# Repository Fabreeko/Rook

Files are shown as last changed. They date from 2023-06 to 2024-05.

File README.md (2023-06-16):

# Rook_Fabreeko
Fabreeko Rook Kit 

https://www.fabreeko.com/products/rook-mk1-by-rolohaun-3d-pre-order?_pos=1&_psq=Roo&_ss=e&_v=1.0

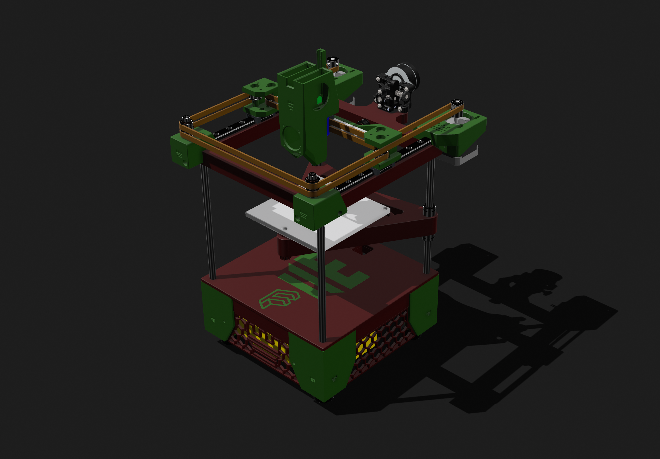
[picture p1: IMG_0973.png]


a derivative of the great work by https://github.com/rolohaun/Rook

We encourage you to use an Initial Startup process like https://docs.vorondesign.com/build/startup/ once you first turn it on. If the stepper_buzz process doesn't yield expected results, you may need to swap the center two wires at one end (I did the motor end) of the wire harness. 

Discord: https://discord.gg/MnxdJcBk

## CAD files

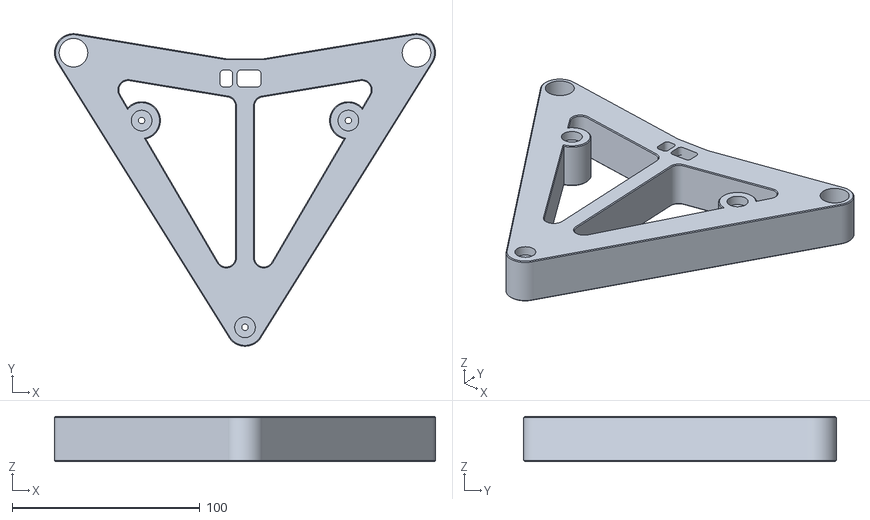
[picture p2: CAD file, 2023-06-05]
STLs/Bed support/Main Bed support.stl
202.7 x 166.3 x 24.0

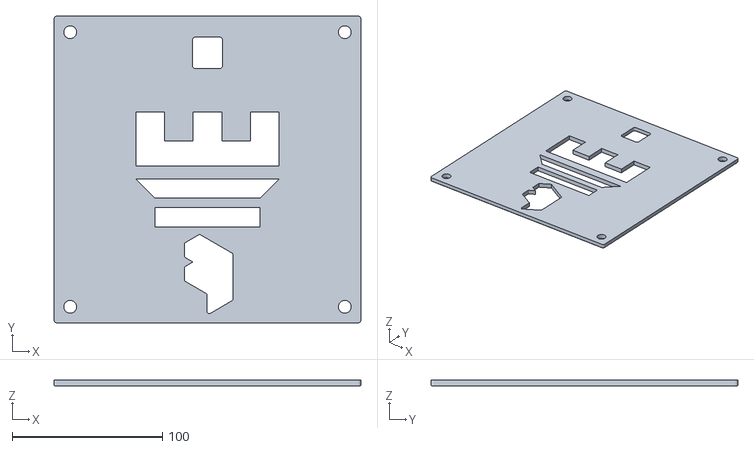
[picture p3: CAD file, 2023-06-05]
STLs/panel/Main panel.stl
204.0 x 204.0 x 4.00

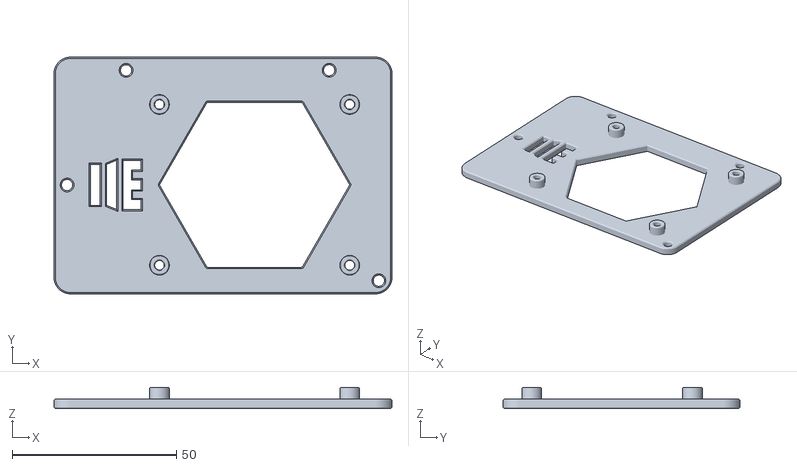
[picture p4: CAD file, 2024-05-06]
STLs/bottom frame/BTT_SKR_E3_v3_to_SKR_Pico_Mount_STL.stl
103.0 x 72.1 x 6.50

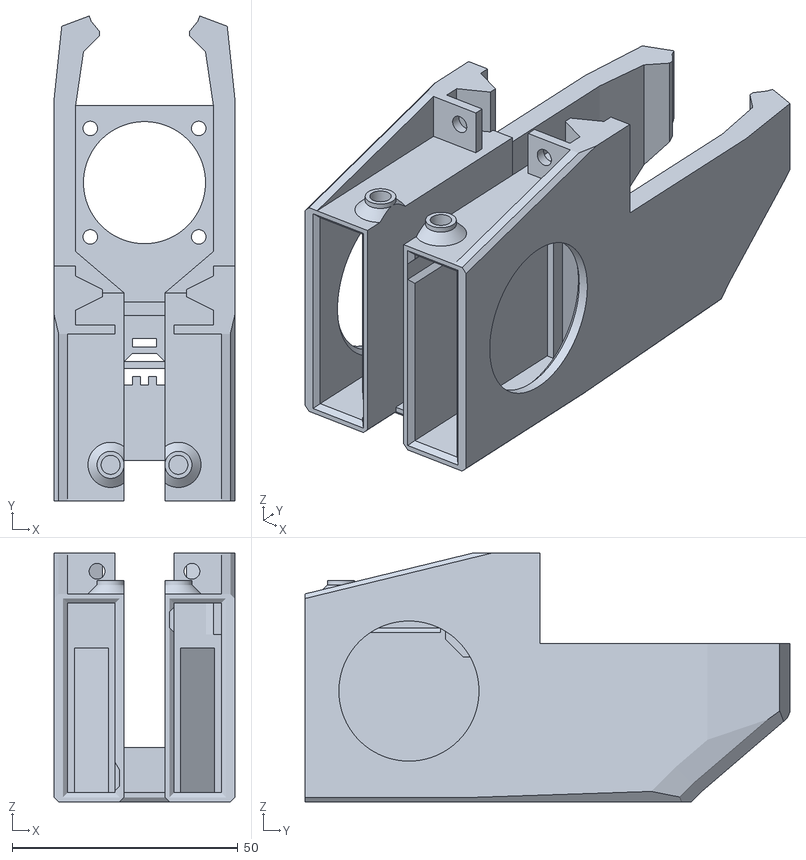
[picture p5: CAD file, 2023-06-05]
STLs/gantry/(a) Cowling.stl
40.0 x 107.3 x 55.0

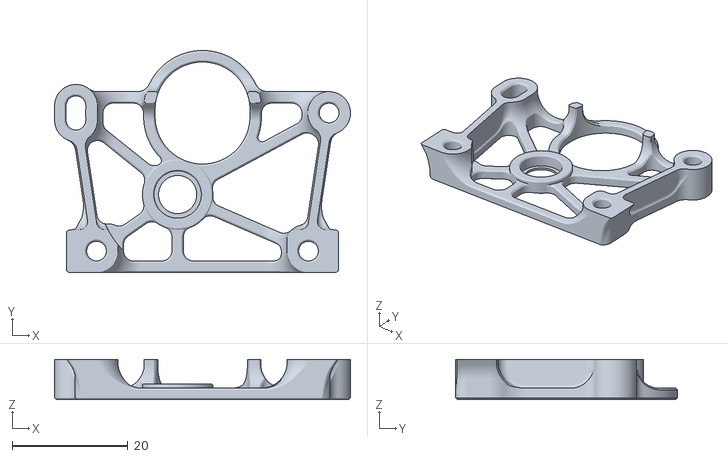
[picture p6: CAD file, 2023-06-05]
STLs/mini Sherpa/Housing rear.stl
51.2 x 38.4 x 7.00

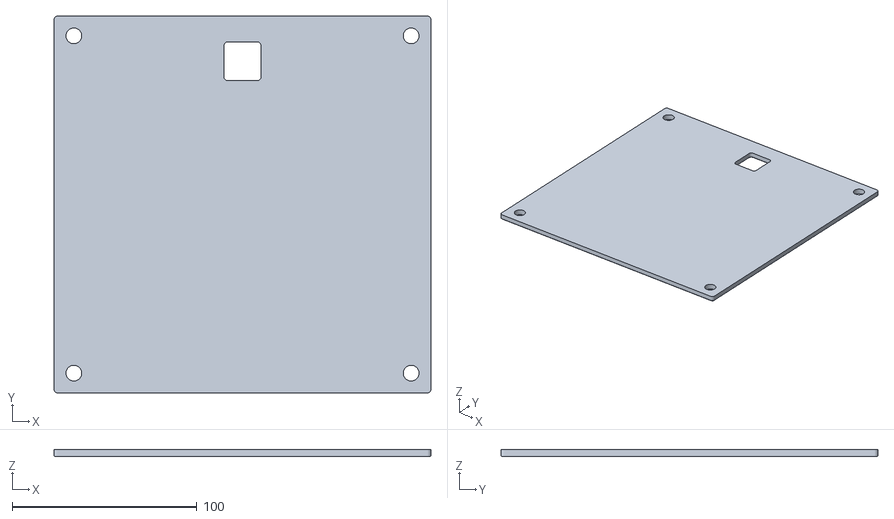
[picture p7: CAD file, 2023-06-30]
STLs/panel/Rook MMU Panel.stl
204.0 x 204.0 x 4.00

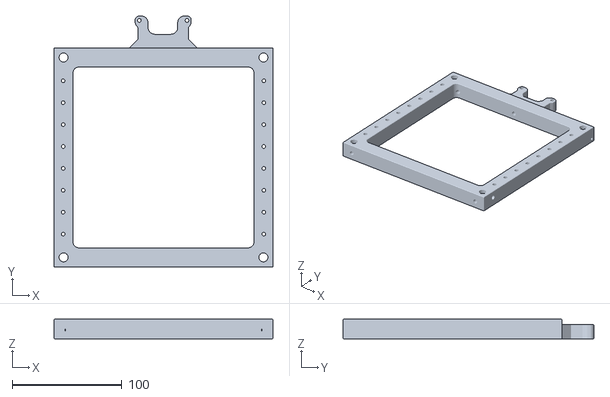
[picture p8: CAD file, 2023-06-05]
STLs/Top Frame/top frame.stl
200.0 x 229.1 x 18.0

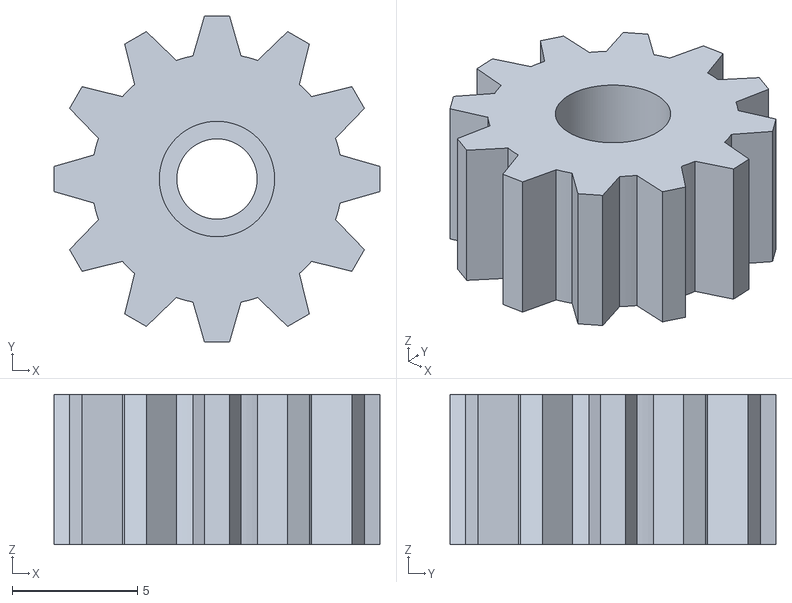
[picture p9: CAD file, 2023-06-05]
STLs/Bed support/Thumb wheelx3.stl
13.0 x 13.0 x 6.00

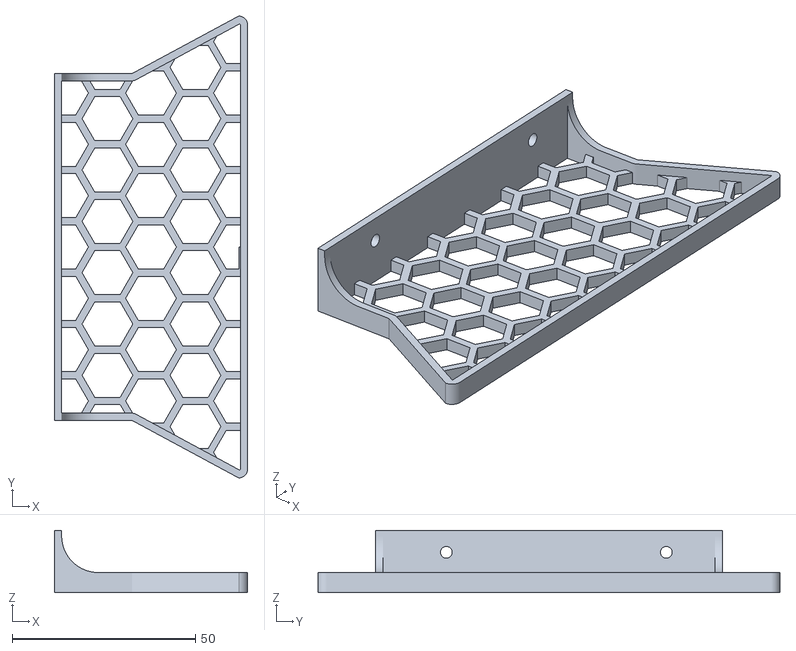
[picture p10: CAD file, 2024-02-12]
STLs/bottom frame/ b_side skirt.stl
52.7 x 126.0 x 17.0

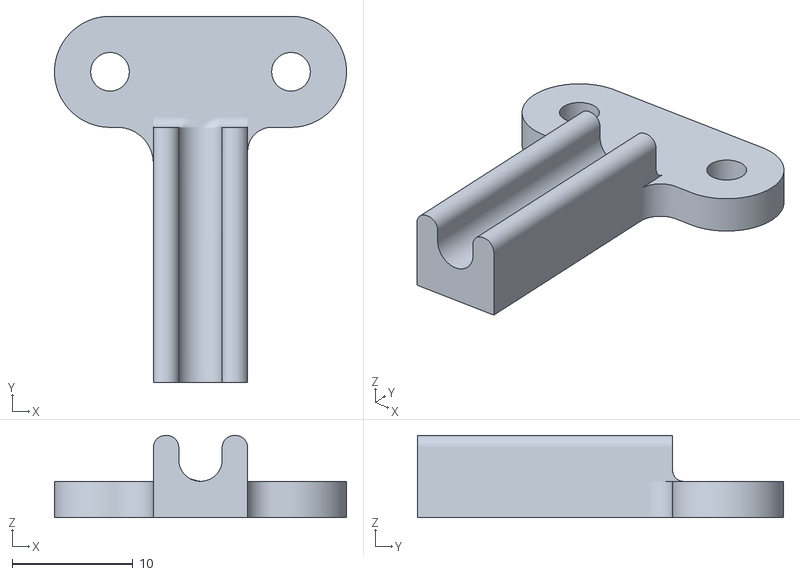
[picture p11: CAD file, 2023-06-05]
STLs/gantry/(a) Stress relief.stl
24.2 x 30.4 x 6.80

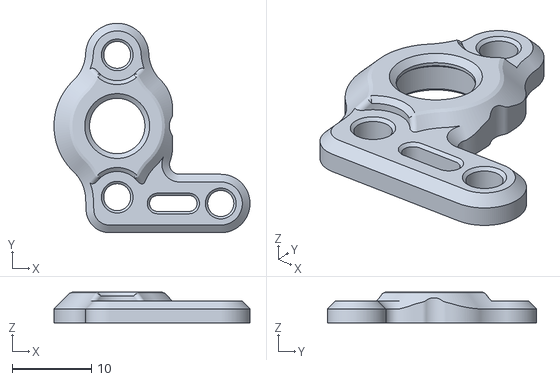
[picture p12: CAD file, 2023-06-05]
STLs/mini Sherpa/(a) Housing front.stl
24.8 x 26.5 x 3.90

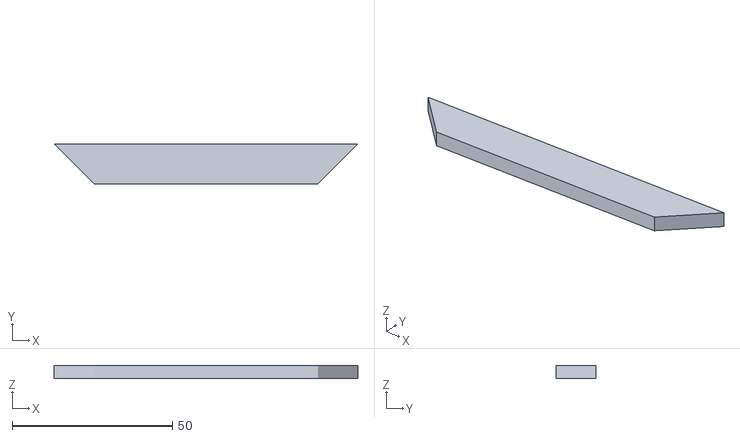
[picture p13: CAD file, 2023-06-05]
STLs/panel/(a) logo_mid.stl
94.8 x 12.5 x 4.00

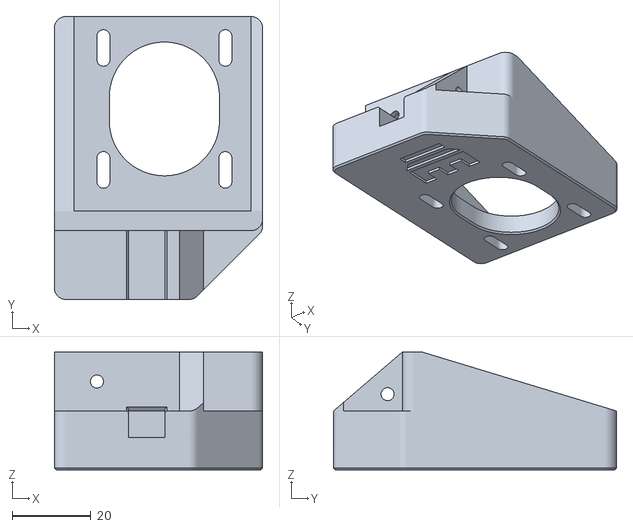
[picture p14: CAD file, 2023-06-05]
STLs/Top Frame/(a) B motor mount.stl
53.0 x 72.0 x 30.0

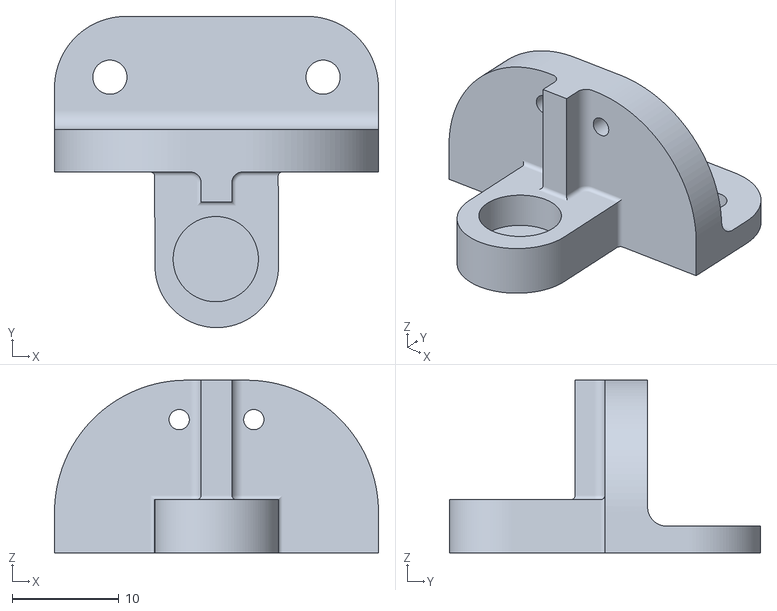
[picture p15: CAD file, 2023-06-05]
STLs/Bed support/Z endstop bracket .stl
30.4 x 29.2 x 16.2

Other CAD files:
STLs/bottom frame/(a) Front left leg.stl
STLs/gantry/(a) Belt clamp.stl
STLs/mini Sherpa/(a) idler arm long.stl
STLs/panel/F Insert 3.stl
STLs/Top Frame/(a) A motor mount.stl
STLs/Top Frame/(a) Gantry.stl
STLs/Top Frame/(a) Left idler mount.stl
STLs/Top Frame/(a) Right idler mount.stl
STLs/bottom frame/(a) Back Left leg.stl
STLs/bottom frame/(a) Front right leg.stl
STLs/bottom frame/(a)Back right leg.stl
STLs/bottom frame/b_Front skirt.stl
STLs/gantry/(a) Hotend Mount.stl
STLs/panel/(a) F Insert 5.stl
STLs/panel/(a) logo_bottom.stl
STLs/panel/(a) logo_top.stl
STLs/panel/F Insert 1.stl
STLs/panel/F Insert 2.stl
STLs/panel/F Insert 4.stl

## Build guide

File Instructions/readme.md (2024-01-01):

# Rook MK1 By Rolohaun 3D
---
### Time to get started! 

Ok - time to take a break.  Go to a different room where you can't see or touch a single piece of the printer. Grab a refreshment, sit down and read through this all the way to the bottom. Once you have read all the way through it, and come back to this point, you can return to the printer. Remember, your camera is on and we can see if you don't do this!

First step is to get all of the heat sets placed. There are 2 different sized heatsets in the kit. Its important to use the shorter heatsets on the rookery and mounting key. If you are not familiar with this, Nero3D has a couple of good YouTube videos on it. 
https://youtube.com/shorts/cyof7fYFcuQ?feature=share

 ### Start by placing heatsets into the lower frame:

Step1

 ### Then place them into the Bed Support, dont forget to place them in the thumbscrews as well (not pictured)



 ### Next, the upper frame



 ### ...and finally, the tool head parts



 ### Next up is attaching the feet to the legs. 
 An M5 nut is captured in the leg and 4 M5X16 SHCS attach the feet.



 ### Attach all four feet to the lower frame as shown using 8 M3x10 SHCS. 



 ### Stand the printer up and insert the four 8mm rods into place. 



 ### This is your first "square and level check". 
 On a known flat surface, make sure the feet don't wobble. Flip it to stand upside down and check for wobbles. This makes sure all the rods are inserted evenly. 
 Grab the lower panel and the inserts. This should be a nice snug fit that can be tapped into place. Assemble all pieces. 



 ### Drop the panel down over the rods. 
 Pay attention to orientation here. 



 ### Insert the bearings into the bed support and center them. 
 They are extra long on purpose to provide more support. Attach the Z endstop in place using two M3x6 SHCS. 



 ### Lower the bed support onto the rear 8mm rods as shown. Note that the Z endstop faces down. 



 ### Attach Y rails to the top frame with 16 M3x20 SHCS. 
 Leave the shuttle keepers in place for now.



 ### Place the top frame on top of the 8mm rods. 
 Make sure it bottoms out on the rods.



 ### Place motor mounts and front idlers on top frame. 
 Two M3x16 BHCS (one each) go in the idlers from the front.  Two M3x10 (one each) attach them from the sides. Two M3X8 SHCS (one each) attach the motor mount from the side into the plastic (be careful not to overtighten/strip these). Two M3x18 SHCS (one each) attach the mount from the rear. 


 ### Attach the linear rail to the X axis.
 Attach the rail to the x-axis using eight M3X12 BHCS with a washer and M3 nut on the back of each. Don't let the shuttle fall of the ends! 



 ### Attach the X axis to the Y rails.
 Attach using three M3x6 SHCS on each side (six total). 



 ### Attach the A/B motors
 Attach the motors to the motor mounts with four M3x10 SHCS (eight total), adjusted all the way towards the front of the printer.  Wires go towards the center. Attach the GT2 pulleys as shown. Pay attention to orientation and height. We will fine tune the height later.


 ### This shows a proper bearing stack assembly for a double bearing stack.  
 Note the two shims in the middle. Always do shim-bearing-bearing-shim on a single. A double is two singles so two shims in the middle. 


 ### Install four single bearing stacks in the X axis using M5x25 SHCS. 





 ### ...and a double bearing stack on each idler using M5x30 SHCS. 


 ### ...and a single stack for the Z belt using an M5x20 SHCS.



 ### The belt path is a standard CoreXY belt path. Study the two pics carefully. One is a cut away and the other is a normal view.  Being methodical here will pay off in the long run. 





 ### Install the Belt Clamp
We will be taking the mount on and off a couple times. It attaches using 4 M3x6 BHCS. The first step will use the full length of the supplied belt. With the teeth facing front, insert one end of the belt through the back of the mounting plate throught the top, right side yellow hole of the blue part in the picture. Fold the belt back over itself so about 25mm overlaps, teeth to teeth. Use a wire tie to temporarily secure it. (Note: my CAD skills and time did not allow me to show the belt loop or teeth so follow the words, not just the picture) 


-  Using the picture above, route the other end through the top belt path all the way around and back through the top left hole from behind.
  - Pull snug and temporarily secure the belt back onto itself.
  - Carefully review your work while looking at the belt path in the picture. Make sure the belt is riding properly on each beating. 

- Cut the belt about 25mm past the securing point. (So you have an extra 25mm). 

- Completely remove the belt.  
  - Lay the piece you just cut on top of the remaining belt and align the ends. The goal is to cut another piece the exact same length, down to the number of teeth. **Making sure there are the same amount of teeth in each belt is vital to print quality**

- Insert each belt through the back of the tool head mount (blue part) from the back on the same side, one top and one bottom.
- Fold each one back on itself, teeth to teeth, just enough to secure them together. (About 25mm). Do this identical for each one, **down to the tooth**. Secure each one to itself with two zip ties.

Loosely attach the tool head mount to the X rail.  Now reroute each belt according the the photos. Push the ends through the back of the tool head mount (might be easier to remove the mount for a minute) and pull tight. Ensure the same amount of teeth are exposed on each belt.  When pulling, pull across the rail and not towards the front as that may break the part. Secure the belts back on to themselves and the mount to the rail. We will tighten later with the A and B motors. Paying attention to cutting the belts the same length, securing them the same, routing them properly and securing the opposite end the same length will help a great deal in initial tuning later. Note that the hotend key is designed such that the belts wont be tight enough to grab the key holes without sliding out. They rely on the friction of the mesh when you fold the belts back onto themselves and secure with a zip-tie.

### Next, mount the Rookery Hotend 
Mount the hotend and secure it to it's mount through the top two holes two M3x16 SHCS. 



### Place this assembly onto the X carriage
Secure it from the back through the bottom hole with one M3X8 BHCS. 




### Place the 4010 fans into the shroud.
Start by routing wires in first and through the access holes in the center. Outflow goes down, inflow faces out. Mount the 3010 fan in place with 4 M3x16 BHCS, washers and M3 nuts.


### Attach Rookery assembly to the carriage
- Mount the entire hotend shroud to the printer by sliding it into place, and secure with 2 M3x6 BHCS. Then and add the stress relief wire mount with 2 more M3x6 BHCS. 
- You may notice there is a wire managemnt tab on your hotend that is getting in the way of the rookery. You can (and should) rotate this to the front of the machine, and route the wires between the fan and the heatsink. You can rotate this by losening the set screw on the front of the hot end.



### Install the Z motor and pulley as shown using 4 M3x12 BHCS. 
The motor should be shifted as far towards the top of the printer as possible to allow for adjustment later.


### Install the Z belt as shown. 
- Use the same process as A/B belts to fasten the belt back on itself.
  - See the cut-away view on how to route each end. 
- Wrap one end around the bed support and secure it back on itself with two zip ties, route as shown all the way around back through the other portion of the bed support.
- Pull tight and secure it to itself, cut off excess. 









### Install the MCU, Fan and (if using this solution) the RPi Zero 2.



### Attach the Z Endstop using M2.5x12 self tapping screws


### Attach screws to Bed
- Attach three m3x50mm SHCSs to the bed by sliding the screw through the hole in the top
- Secure the screws to the bed using an M3 washer and nut on the under side of the bed.
### Attach Bed to Frame
- Slide included yellow bed springs over the screws
- Secure the bed to the bed mount using the three thumbscrews we printed.
- Finally, Install the thermistor in the bed, it screws into the hole in the bottom center.

### Push the power port in place.


### Attach the skirts
The skirts will be the last printed parts to attach. Leave them off for now, but this shows where they go. You will need to do all of the wiring first. The area highlighted in green are wire tie paths for small wire ties to help with wire management as you finish up. 


### Attach the PSU
We suggest getting all the startup checks and tuning with the PSU sitting next to the printer until you are fairly certain that all is well. When you are all set, add the skirts and finally the PSU. The PSU mounts through the holes in the front feet, and will sit "below" your previously installed electronics.

### Wiring
- The wiring process is tedious for sure, but also straight forward, especally if you have previously built a printer.
- Use the MCUs github and follow the printer.cfg here to place all the wires correctly. 
- If you have not done wiring for a printer before, watching a couple of videos on YouTube may help. 

### Mini Sherpa Extruder
- The last thing for you to do is to build the extruder. The Extruder we are using is the mini sherpa. Please use the files in this repo, as the stock mini sherpa **does not work/properly mount with our bowden setup.** That said, the build process should be the same, and can be found in here. https://github.com/Annex-Engineering/Sherpa_Mini-Extruder/tree/master/Build_Instructions
  
- Note that some kits ship with a gear that is too long.
  - If, when assembling, you notice that the filament path in the print cannot line up with the one on the gear, its because the plastic spacing on the base of the white gear is too long. You may need to widdle this down by ~1mm (photos and fix credit Kwisatz_Nine9 on discord)


 

After building the mini-sherpa, mount it to the back of the machine and run a bowden tube between the extruder and the hot end.

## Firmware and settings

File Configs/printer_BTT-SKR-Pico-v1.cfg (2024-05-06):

# This file contains common pin mappings for the BIGTREETECH SKR Pico V1.0
# To use this config, the firmware should be compiled for the RP2040 with
# USB communication.

# The "make flash" command does not work on the SKR Pico V1.0. Instead,
# after running "make", copy the generated "out/klipper.uf2" file
# to the mass storage device in RP2040 boot mode

## Rolohaun3D Fabreeko Rook Mk1 SKR Pico V1.0 config

## *** THINGS TO CHANGE/CHECK: ***
## MCU path                                                                     [mcu] section
## Z and Extruder motor currents                                                [tmc2209 stepper_*] sections. Uncomment the stepper motor you have
## Full steps per rotation for Extruder                                         [extruder] section
## Thermistor types                                                             [extruder] and [heater_bed] sections - See https://www.klipper3d.org/Config_Reference.html#common-thermistors for common thermistor types
## Motor currents                                                               [extruder] [stepper] and [_HOME_X/Y] macro sections
## PID tune                                                                     [extruder] and [heater_bed] sections
## Fine tune E steps                                                            [extruder] section
## For more info                                                                check https://docs.vorondesign.com/build/startup/#v0

# See docs/Config_Reference.md for a description of parameters.
[include mainsail.cfg]
[include sensorless.cfg]

[virtual_sdcard]
path: /home/pi/printer_data/gcodes
on_error_gcode: CANCEL_PRINT

[force_move]
enable_force_move: true

#[include KlipperScreen.conf]

#[include timelapse.cfg]

[exclude_object]


[pause_resume]

[mcu]
serial: /dev/serial/by-id/usb-Klipper_stm32g0b1xx_2A00440007504B5735313920-if00 # UPDATE WITH YOUR INFO



[printer]
kinematics: corexy
max_velocity: 300
max_accel: 10000
max_z_velocity: 300
max_z_accel: 100

#[safe_z_home]
#home_xy_position: 115,115 # Change coordinates to the center of your print bed
#speed: 50
#z_hop: 10                 # Move up 10mm
#z_hop_speed: 5


# A Stepper connected to XM
[stepper_x]
step_pin: gpio11 # checked
dir_pin: gpio10   # checked
enable_pin: !gpio12 # checked
microsteps: 32 # checked
rotation_distance: 40 # checked
endstop_pin: tmc2209_stepper_x:virtual_endstop
homing_retract_dist: 0
position_endstop: 110
position_max: 110
homing_speed: 50

[tmc2209 stepper_x]
diag_pin: ^gpio4 # use the same pin that was previously the endstop_pin!
driver_SGTHRS: 135
uart_pin: gpio9 # checked
tx_pin: gpio8
uart_address: 0
run_current: 0.75
sense_resistor: 0.110
stealthchop_threshold: 1



# B Stepper connected to YM
[stepper_y]
step_pin: gpio6 # checked
dir_pin: gpio5 # checked
enable_pin: !gpio7 # checked
microsteps: 32 # checked
rotation_distance: 40 # checked
endstop_pin: tmc2209_stepper_y:virtual_endstop
homing_retract_dist: 0
position_endstop: 109
position_max: 109
homing_speed: 50

[tmc2209 stepper_y]
diag_pin: ^gpio3 # use the same pin that was previously the endstop_pin!
driver_SGTHRS: 145
uart_pin: gpio9
tx_pin: gpio8
uart_address: 2
run_current: 0.75
sense_resistor: 0.110
stealthchop_threshold: 1

[stepper_z] #Connected to Z1
step_pin: gpio19
dir_pin: gpio28
enable_pin: !gpio2
microsteps: 16
rotation_distance: 40
# endstop_pin: ^gpio26
position_endstop: 100
endstop_pin: gpio26
position_max: 100
position_min: -1.5

[tmc2209 stepper_z]
uart_pin: gpio9
tx_pin: gpio8
uart_address: 1
run_current: 0.580
hold_current: 0.500
stealthchop_threshold: 1

[extruder] # connected to EM
step_pin: gpio14
dir_pin: gpio13
enable_pin: !gpio15
microsteps: 16
rotation_distance: 3.7710
nozzle_diameter: 0.400
filament_diameter: 1.750
heater_pin: gpio23
sensor_type: Generic 3950
sensor_pin: gpio27  		#TH0
#control: pid
#pid_Kp: 21.527
#pid_Ki: 1.063
#pid_Kd: 108.982
min_temp: 0
max_temp: 250

[tmc2209 extruder]
uart_pin: gpio9 
tx_pin: gpio8
uart_address: 3
run_current: 0.75
#hold_current: 0.500
stealthchop_threshold: 0

[heater_bed]
heater_pin: gpio21 #checked
sensor_type: ATC Semitec 104GT-2 #checked
sensor_pin: gpio26 #checked
#control: pid
#pid_Kp: 54.027
#pid_Ki: 0.770
#pid_Kd: 948.182
min_temp: 0
max_temp: 130

[temperature_fan controller_fan] # electronics fan connected to FAN3
pin: gpio20
#heater: heater_bed
#heater_temp: 45.0
sensor_type: temperature_host
control: watermark
min_temp: 0
max_temp: 100
target_temp: 30

[heater_fan hotend_fan] 		# Hotend fan connected to FAN2
pin: gpio18
max_power: 1.0
kick_start_time: 0.5
heater: extruder
heater_temp: 50.0

[fan] 							# PartCooling fan connected to FAN1
pin: gpio17


## RPi or CB1 Temp
[temperature_sensor RPi]
sensor_type: temperature_host
min_temp: 10
max_temp: 100

## MCU Temp
[temperature_sensor MCU_temp]
sensor_type: temperature_mcu
min_temp: 0
max_temp: 100

[mcu rpi]
serial: /tmp/klipper_host_mcu

[adxl345]
cs_pin: rpi:None

[resonance_tester]
accel_chip: adxl345
probe_points:
    55, 55, 20  # an example



#####################################################################
# Macros
#####################################################################



[homing_override]
axes: xyz
gcode:
  {% set home_all = 'X' not in params and 'Y' not in params and 'Z' not in params %}

  {% if home_all or 'X' in params %}
    _HOME_X
  {% endif %}

 {% if home_all or 'Y' in params %}
    _HOME_Y
  {% endif %}
  
  {% if home_all or 'Z' in params %}
    FORCE_MOVE STEPPER=stepper_z DISTANCE=-8 VELOCITY=25
    G28 Z
    G90 
    G1 X54 Y54 Z25
  {% endif %}


[bed_screws]
screw1: 54,5
screw1_name: front screw
screw2: 0,108
screw2_name: back left
screw3: 108,108
screw3_name: back right


[gcode_macro PRINT_START]
#   Use PRINT_START for the slicer starting script - please customize for your slicer of choice
gcode:
    G28                            ; home all axes
    G90                            ; absolute positioning    
    #G1 Z-20 F3000                   ; move nozzle away from bed
   
[gcode_macro PRINT_END]
#   Use PRINT_END for the slicer ending script - please customize for your slicer of choice
gcode:
    M400                           ; wait for buffer to clear
    G92 E0                         ; zero the extruder
    G1 E-4.0 F3600                 ; retract filament
    G91                            ; relative positioning

    #   Get Boundaries
    {% set max_x = printer.configfile.config["stepper_x"]["position_max"]|float %}
    {% set max_y = printer.configfile.config["stepper_y"]["position_max"]|float %}
    {% set max_z = printer.configfile.config["stepper_z"]["position_max"]|float %}

    #   Check end position to determine safe direction to move
    {% if printer.toolhead.position.x < (max_x - 20) %}
        {% set x_safe = 20.0 %}
    {% else %}
        {% set x_safe = -20.0 %}
    {% endif %}

    {% if printer.toolhead.position.y < (max_y - 20) %}
        {% set y_safe = 20.0 %}
    {% else %}
        {% set y_safe = -20.0 %}
    {% endif %}

    {% if printer.toolhead.position.z < (max_z - 2) %}
        {% set z_safe = 2.0 %}
    {% else %}
        {% set z_safe = max_z - printer.toolhead.position.z %}
    {% endif %}

    G0 Z{z_safe} F3600             ; move nozzle up
    G0 X{x_safe} Y{y_safe} F20000  ; move nozzle to remove stringing
    TURN_OFF_HEATERS
    M107                           ; turn off fan
    G90                            ; absolute positioning
    G0 X54 Y{max_y} F3600          ; park nozzle at rear
  
  
[gcode_macro LOAD_FILAMENT]
gcode:
   M83                            ; set extruder to relative
   G1 E30 F300                    ; load
   G1 E15 F150                    ; prime nozzle with filament
   M82                            ; set extruder to absolute
    
	
[gcode_macro UNLOAD_FILAMENT]
gcode:
   M83                            ; set extruder to relative
   G1 E10 F300                    ; extrude a little to soften tip
   G1 E-40 F1800                  ; retract some, but not too much or it will jam
   M82                            ; set extruder to absolute

#*# <---------------------- SAVE_CONFIG ---------------------->
#*# DO NOT EDIT THIS BLOCK OR BELOW. The contents are auto-generated.
#*#
#*# [heater_bed]
#*# control = pid
#*# pid_kp = 69.398
#*# pid_ki = 0.993
#*# pid_kd = 1212.736
#*#
#*# [extruder]
#*# control = pid
#*# pid_kp = 18.137
#*# pid_ki = 1.656
#*# pid_kd = 49.651
#*#
#*# [input_shaper]
#*# shaper_type_x = mzv
#*# shaper_freq_x = 73.0
#*# shaper_type_y = mzv
#*# shaper_freq_y = 71.2

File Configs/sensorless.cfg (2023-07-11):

[gcode_macro _HOME_X]
gcode:
    # Always use consistent run_current on A/B steppers during sensorless homing
    {% set RUN_CURRENT_X = printer.configfile.settings['tmc2209 stepper_x'].run_current|float %}
    {% set RUN_CURRENT_Y = printer.configfile.settings['tmc2209 stepper_y'].run_current|float %}
    {% set HOME_CURRENT = 0.82 %}
    SET_TMC_CURRENT STEPPER=stepper_x CURRENT={HOME_CURRENT}
    SET_TMC_CURRENT STEPPER=stepper_y CURRENT={HOME_CURRENT}

    # Home
    G28 X
    # Move away
    G91
    G1 X-10 F4000
    
    # Wait just a second… (give StallGuard registers time to clear)
    G4 P1000
    # Set current during print
    SET_TMC_CURRENT STEPPER=stepper_x CURRENT={RUN_CURRENT_X}
    SET_TMC_CURRENT STEPPER=stepper_y CURRENT={RUN_CURRENT_Y}

[gcode_macro _HOME_Y]
gcode:
    # Set current for sensorless homing
    {% set RUN_CURRENT_X = printer.configfile.settings['tmc2209 stepper_x'].run_current|float %}
    {% set RUN_CURRENT_Y = printer.configfile.settings['tmc2209 stepper_y'].run_current|float %}
    {% set HOME_CURRENT = 0.82 %}
    SET_TMC_CURRENT STEPPER=stepper_x CURRENT={HOME_CURRENT}
    SET_TMC_CURRENT STEPPER=stepper_y CURRENT={HOME_CURRENT}

    # Home
    G28 Y
    # Move away
    G91
    G1 Y-10 F4000

    # Wait just a second… (give StallGuard registers time to clear)
    G4 P1000
    # Set current during print
    SET_TMC_CURRENT STEPPER=stepper_x CURRENT={RUN_CURRENT_X}
    SET_TMC_CURRENT STEPPER=stepper_y CURRENT={RUN_CURRENT_Y}

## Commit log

2023-06-05 Rename printer.cfg 3.txt to printer.cfg
    [printer.cfg]
2023-06-18 Instructions draft (#1)
    * Create readme.md
    * Update readme.md
    * Update readme.md
    * Update readme.md
    * Update readme.md
    * Update readme.md
    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
    [(a) Front left leg.stl]
2023-06-25 Added CAD
2023-06-30 Update to the MMU Panel
    Less change of colors. Switches to solid color after 1MM
    [Rook MMU Panel.stl]
2023-07-01 Update heatsets
2023-07-01 Added weep holes for rods
2023-07-11 Added Sensorless.cfg
    [sensorless.cfg]
2023-12-30 Update readme.md
    Fixed error in bolt size
2024-01-01 Update readme.md (#2)
    Updated readme to include information I needed when building the printer.
2024-02-12 Rename Rook side skirt.stl to b_side skirt.stl
    [b_side skirt.stl]
2024-05-06 Add SKR Pico V1 support by Delmar (#3)
    This commit adds the printer.cfg file, as well as a bottom mount.
    This work was contributed by Delmar (Fabreeko Discord).
    [BTT_SKR_E3_v3_to_SKR_Pico_Mount_STL.stl, printer_BTT-SKR-E3-Mini-v3.cfg, printer_BTT-SKR-Pico-v1.cfg]
